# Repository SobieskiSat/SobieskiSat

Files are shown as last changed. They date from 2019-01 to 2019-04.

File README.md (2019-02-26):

# Welcome to SobieskiSat Main repository
## What is SobieskiSat?
We are a group of students from the II High School in Kraków. We got qualified for the CanSat competition, which is organised by the ESERO. Our mission is to build a can-sized atmospheric probe. The objective of CanSat competition is to develop a lot of small probes which can be used for scientific research and advancing technology.

## What is your mission?
Our mission is to build and launch a can-sized atmospheric probe, which will be equipped with basic sensors like temperature, humidity and  pressure, and also with more advanced modules like an air quality meter. In our project we also use advanced GPS positioning and RF communication using LoRa protocol.

## Repository Structure
SobieskiSat is a complex project that requires work in many fields including software, electronics, 3D-Design. That's why we divied this repository into a few directories:
  - ['docs'](docs/) - project documentation
  - ['gerber'](gerber/) - PCB gerber files
  - ['logs'](logs/) - test flights logs
  - ['models'](models/) - 3D designs
  
 ## Follow our project
 You can follow us on [facebook](https://www.facebook.com/SobieskiSat/) or visit our website <https://sobieskisat.pl/en/>
 
 ## Contact
 Contact us on Facebook or by email:<info@sobieskisat.pl>

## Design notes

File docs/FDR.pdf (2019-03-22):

# Final Design Review

### for CanSat competition

### Team

## SobieskiSat

Changelog | 2
Introduction | 3
Team composition | 3
Available resources and time management | 4
Mission overview | 4
Primary mission | 4
Secondary mission | 5
Probe description | 6
Introduction | 6
Components description | 6
Microcontroller board | 6
Batteries | 6
Atmospheric pressure and temperature sensor | 6
Particulate matter sensor | 7
Humidity sensor | 7
GPS module | 7
IMU module | 8
Gases sensor | 8
Buzzer | 9
Photoresistor | 9
Measurements | 9
Recovery system | 10
Mechanical design | 11
Weight | 11
Case | 12
Parachute | 12
Transmitting antenna | 13
Electrical design | 14
Daughterboard design | 14
Power consumption | 15
Software design | 16
System structure | 16
Data gathering | 17
Event logging and timers | 17
Data compression during radio transmission | 17
Ground station | 18
Radio receiving | 18
Ground Station Interface | 19
Landing prediction feature | 20
Data Analyzing Software | 20
Test campaign | 21
Kraków, Poland, 13.01.2019 | 1

Radio transmission tests | 21
Drone drop tests | 21
Thermovision tests - heat visualisation | 24
Project summary | 25
Resource management | 25
Budget and costs | 25
CanSat Value | 26
Sponsors | 27
Documentation | 28
Social media & promotion | 28
Facebook | 28
Radio promotion | 29
Articles | 29
Summary | 30
Education | 30
GitHub Repository | 30
Timeline | 30
Cansat Characteristics | 40

# 1. Changelog

- PDR
- Initially we planned to use an outside communication module with a chip supporting LoRa, but since it is already in CanSat kit provided to us, it was deemed unnecessary and we opted to came with some other ideas for the secondary mission.
- As of the PDR, our main goal in the secondary mission has changed. Now we are going to collect humidity and video data alongside PM density.
- In addition to the main goal of the secondary mission we also added plans to develop a descension assistance system (DAS).
- CDR
- We decided to leave out the camera because we could not find any suitable one for our needs and compatible to our board.
- We’ve updated our component list with final components we chose according to our financial capabilities and electrical requirements.
- Mission stages from PDR were modified due to software development.
- DAS (Descension Assistance System) was delayed due to prototyping restrictions and ultimately its goal was changed to predict the landing site using linear regression.

- We found that LM35 thermometer was outputting unusable disturbed data while sending via radio. Because of that we use BMP280 as our main thermometer.
- We changed GPS module to Adafruit Ultimate GPS, it includes RTC module so one planned in PDR is not needed anymore.
- Particulate matter sensor was changed to SPS30.
- FDR
- Added a new MQ-9 sensor to help analysis in secondary mission.
- We decided to increase promotion of our project in both social and traditional media.
- We finished a lot more drone drop tests than we expected to carry out at the beginning, for better analysis of data
- Descension Assistance System was finally examined and implemented into our main code.
- No more big changes were executed - we focused on developing the systems we decided to use before writing CDR

# 2. Introduction

## 2.1. Team composition

Our team consists of 5 students and our tutor, all of us are attending High School No. 2 named after King John III Sobieski in Kraków. Aleksandra Musiał - Our tutor, CS teacher and also an administrator at our school’s 3D printing laboratory.
- Jakub Czarny - Team leader & Electro-mechanical designer. His primary role is managing our progress and mission but he also specializes in electronic design and is responsible for choosing components according to our financial and electrical constraints. He is also our 3D designer.
- Andrzej Szablewski - PR spokesperson, he takes care of all PR related missions like finding sponsors, media as well as managing and updating our social media. He also works on programming and testing.
- Maciej Gamrot - High-Level Developer, he is responsible for main system development and communication with ground station. He also works on machine learning, look after our repository and develops our website.
- Damian Legutko - Embedded Developer, his job is to write code for managing data retrieved from sensors, designing backup procedures. On top, Damian designs graphical parts of our project when needed.
- Krzysztof Parocki - Digital Media Creator, he makes a photo-documentation of our progress. He also records and cuts movies based on our creation process. His work is used to promote our project in social media. He also helps with facebook site managing, testing prototypes and organizing.

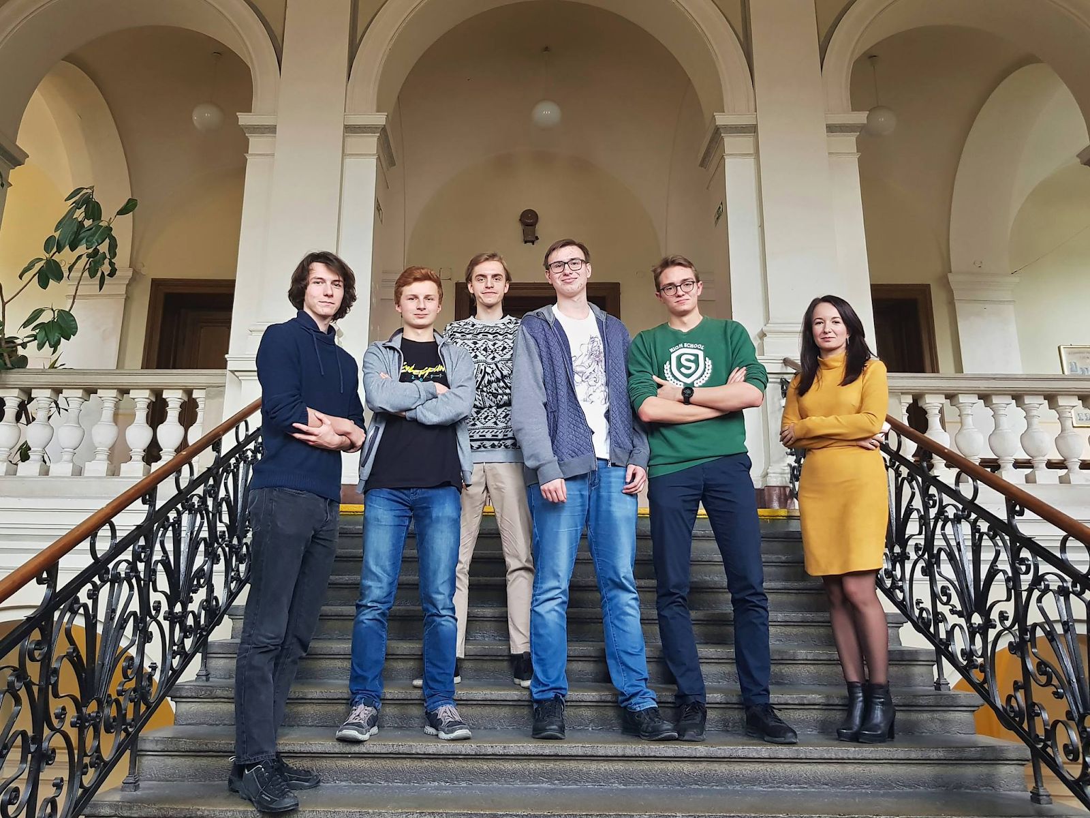
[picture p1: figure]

## 2.2. Available resources and time management

We’ve established cooperation with our school that provided us a classroom, where we hold our meetings and 3D printing lab that is under our tutor’s management. We have access to all the tools needed for the project in a public workshop - Hackerspace Kraków. Outside of the school we work on our own as well as in group through communication apps like Messenger and Discord. We meet once a week in our classroom to summarize the previous week and divide tasks for the next few days. A few weeks before completing FDR we were meeting once a week and testing our CanSat with professional drone operator.

## 2.3. Mission overview

### 2.3.1. Primary mission

CanSat mission is divided into few stages. Because of the importance of primary mission, mission stages are dependent on the time from hardware oscillator clock and photoresistor, secondary mission readings are used only as reference.
- Initialization
During Initialization, software will diagnose every component and save received data in log files on SD card. Checking if everything is working properly would prevent from errors that might occur during the mission. In this stage Can should be standing still on a flat surface for about 3 seconds because few sensors inside would be calibrating.
- Await
The Can will wait for being placed inside the rocket. Probe will occasionally collect sensor data and photoresistor readings will indicate if is put in tray and trigger next stage.
- Launch
Except for light intensity, acceleration values from IMU module would be used as reference to mission stage. Sudden acceleration during lift might cause electrical components to behave in unexpected way, to avoid possible errors most of them will go into sleep mode. If Can could not receive any data after estimated time goes into next stage.
- Fall
As a main part of primary mission, in this stage probe will collect data from all sensors, save them to SD card and send via radio.
- Recovery
Probe goes into recovery stage after estimated time or when it detects landing via accelerometer, gyroscope or GPS. It waits to be found by searching team but still is collecting data and sending radio signals.

### 2.3.2. Secondary mission

Our main goal in the secondary mission is to gain first information about atmosphere quality, disasters, and also volcanic activity. Using sensors like temperature, pressure, humidity, particulate matter density sensor as well as flammable gases and carbon monoxide sensor we can initially determine if the local atmosphere is suitable for the existence of life. Our idea in case of volcanic activity is based on dropping the satellite inside the volcano, while it’s dormant.
Particulate matter density and humidity can be used for controlling and predicting volcanic activity. Particulate matter is a very important factor in our secondary mission. Dust intensity determines chances of survival for both animal and human beings. High densities are very dangerous for life and are a direct information that the region needs evacuation. Other factors like temperature and humidity are also important as an information about life conditions. Our system can be used in fires as well as other natural disasters. The whole probe is supposed to output the collected data for the processing to happen on the ground. This allows us to quickly adapt to whatever is needed and analyze the data thoroughly.

As for launching the probe in finals we expect to test all systems and check for errors as we don’t predict the army range will output dangerous data signalyzing any disasters. The whole point of the probe is life-sensitive data collection which can be interpreted in many different ways.
In addition we will use landing site prediction software to help us understand where we are measuring and assist the primary mission recovery.

# 3. Probe description

## 3.1. Introduction

The whole probe fits in our 3D printed case. We decided to name it “Znicz1” because of the shape of our case. Our list of electrical components is now final when it comes to primary mission components and matches our needs and requirements. Every planned sensor and its function is described below.

## 3.2. Components description

### 3.2.1. Microcontroller board

We managed to test the CanSat Kit microcontroller board and decided to use it inside the probe due to its big capabilities. It completely fulfills our needs and no board change is needed.

Current status: Tested and ready

### 3.2.2. Batteries

We chose to go with 2600mAh modules (ICR18650-26FM) because we found a particular seller which would pre-weld them to a tin strip resulting in a 3P configuration of 7800mAh. This is still a massive battery pack that after a few hours of testing communication its voltage went down just 0.04V and will surely last long enough for the whole flight. Probe includes battery charger and protection module -TP4056.

Current status: Tested and ready

### 3.2.3. Atmospheric pressure and temperature sensor

This sensor fulfills all primary mission data gathering requirements, from received data we are able to calculate altitude of falling Can. The BMP280 provided with the CanSat Kit works just fine through the I

2C interface and we haven’t encountered any problems during tests. It’s also working as our main thermometer, because it’s much more stable and calibrated than the LM35. Beside its obvious function, we will use it for getting exact altitude.

Expected results: Change in temperature and pressure gives information about basic air properties and altitude. We will combine temperature with altitude. Also by this we can get information about potential disaster.

Current status: Tested and ready

### 3.2.4. Particulate matter sensor

The particulate matter sensor is our main focus in the secondary mission. Basing on data collected from this sensor it is possible to examine life conditions. We opted for the SPS30 which provides us high sampling rate of 1Hz that erases the need for slower descension.

Expected results: We expect some air pollution during final competition. It is really hard to predict the values of the pollution, but we know that on significant heights air pollution is low.

Current status: Tested and ready

### 3.2.5. Humidity sensor

Air humidity values would be used in secondary mission to predict possible fires. Very low humidity is often main cause of those disasters.
We found DHT22 sensor most suitable for our needs, it combines high precision and fast update compared to other humidity sensors.

Expected results: We expect change in humidity due to different weather. We will also analyze it in terms of altitude.

Current status: Tested and ready

### 3.2.6. GPS module

We decided to buy the Adafruit Ultimate GPS module based on MTK3339 chip. It was more expensive than our initial choice but its capabilities and big community support made it a best option. It also provided us with a RTC powered by a backup battery. We use it not only to get the exact location but also to get the altitude. It's the second source of this variable, by that we can check our data and make sure that it's correct.

Expected results: From our GPS module we will get exact position and altitude. We restricted expected values of longitude, latitude and altitude in order to get only correct values.

Current status: Tested and ready

### 3.2.7. IMU module

Accelerometer readings from this module could be used to predict earthquakes and avalanches.
Additionally IMU module will give us information about Can momentum additionally it is very useful during tests. We plan to use it when determining landing spot.
With use of special library we managed to get it working as intended. Kalman filters and Magdwick algorithm (inside DMP) used in the library give us very accurate data.

Expected results: The IMU is currently used as a backup in calculating a wind vector and we expect to see at least the full flight recorded in 9 axis.

Current status: Tested and ready

### 3.2.8. Gases sensor

Sensor responsible for this functionality is the MQ-9 module. It is sensitive for carbon monoxide (CO) as well as flammable gases. We predict that we won’t exceed the alarm levels of these gases during the mission, but this sensor is a supplement for the theoretical aspects of our secondary mission.

Expected results: Probably we won’t exceed the alarm levels of flammable gases or carbon monoxide concentration, we will get information about it live.

Current status: Tested and ready

### 3.2.9. Buzzer

The buzzer was implemented on our first PCB with a transistor as to not overload the digital pins of the microcontroller. It’s working just as expected, helping us to locate it after landing(It’s hearable from about 7-10m) and signal that the Can is working.

Expected results: We hope it will help finding our satellite after landing. It’s hearable from about 7-10m.

Current status: Tested and ready

### 3.2.10. Photoresistor

We can get information about CanSat mission stage in a very tricky way, thats by implementing photoresistor. When probe is outside the rocket it detects big amounts of light, if is inside a tray and is covered, no light shines onto photoresistor. We proved this concept during tests, Cansat was elevated inside 'Pringles’ can and ejected with special mechanism attached to drone.

Expected results: We expect that photoresistor will give us information about our can. We will know is it inside or outside the rocket.

Current status: Tested and ready

## 3.3. Measurements

Table below presents data that will be gathered during the mission. Minimum and maximum columns represent predicted values to be received. Readings precision is presented in Significant figures column with format: [before ; after decimal point] in base 10.
Sensor | Reading variables | Minimum | Maximum | Significa nt figures | Samplin g time [ms]
2C) BMP280 (I | Pressure | 600 hPa | 1100 hPa | 4 ; 1 | 40
| Temperature | -10°C | 40°C | 2 ; 1 | 40

Adafruit Ultimate GPS (UART) | Latitude 1 | 49,00° | 52,00° | 2 ; 7 | 1000
| Longitude 1 | 14,07° | 24,09° | 2 ; 7 | 1000
| Altitude | 0 m | 3000 m | 4 ; 1 | 1000
| Clock | mission start time | mission end time | - 1000
DHT22 (Digital communication) | Humidity | 0 % | 100 % | 2 ; 0 | 2000
| Temperature | -10°C | 30°C | 2 ; 1 | 2000
SPS30 (UART) | Mass concentration | 0.3 μg/m³ | 100 μg/m³ | 2 ; 1 | 1000
| Number Concentration | 0.3 1/cm³ | 10 1/cm³ | 1 ; 1 | 1000
MPU 9250 (I 2C) | Tilt | 0° | 360° | 3 ; 2 | 20
| Acceleration | 0 g | 4 g | 1 ; 2 | 20
| Magnetic orientation | 0° | 360° | 3 ; 0 | 30
Photoresistor (Analog) | Light intensity | 0 lux | 10 lux | 1 ; 2 | 10
MQ 9 (Analog) | Flammable gases and carbon monoxide | 0 | 1024 | 4; 0 | 10

1Minimum and maximum values of GPS location are set to Poland boundaries. During the real mission they would not reach further than few kilometres from start. This allows us to compress data more effectively

## 3.4. Recovery system

As described in 3.5 and 3.5.3 we are using a parachute made by us and then calculated and tested for falling with a speed of 9m/s. It’s attached to the body with 8 strings with a holding strength of 60kg. They are attached by pinching them through 8 holes and tying a knot. So far our test have proven this design successful.
The main power switch is located at the bottom and is a simple bistable slide switch. (See 3.5)

## 3.5. Mechanical design

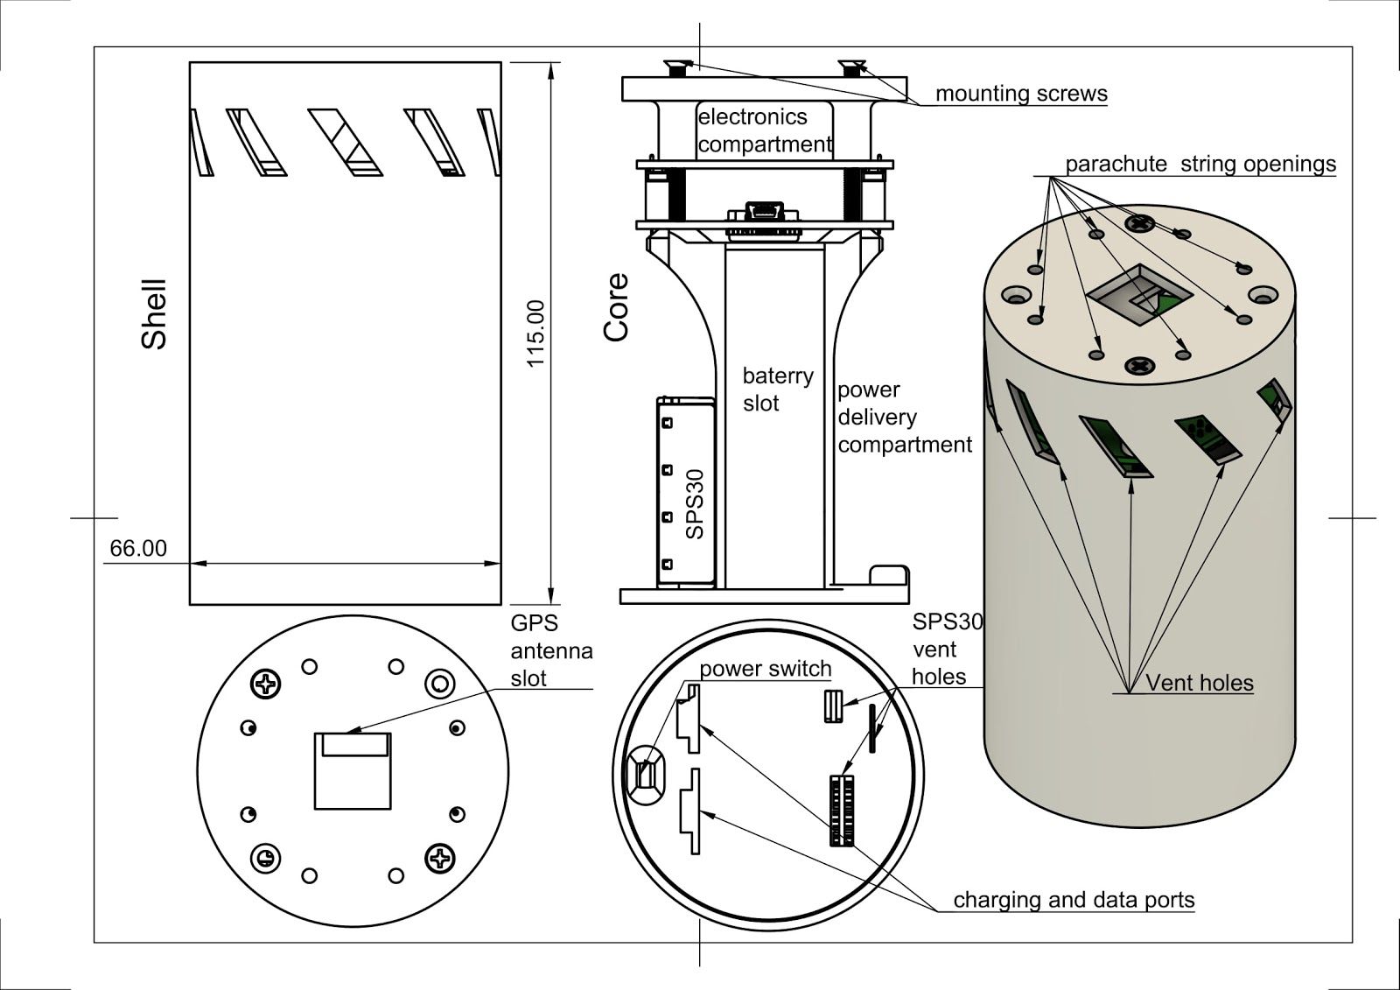
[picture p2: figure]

Open link to the full assembly: https://a360.co/2CFqlhm

### 3.5.1. Weight

Our full assembly was weighed firstly on a kitchen scale then in our school chemistry lab and both reported it being safely under 350g, about 336g.

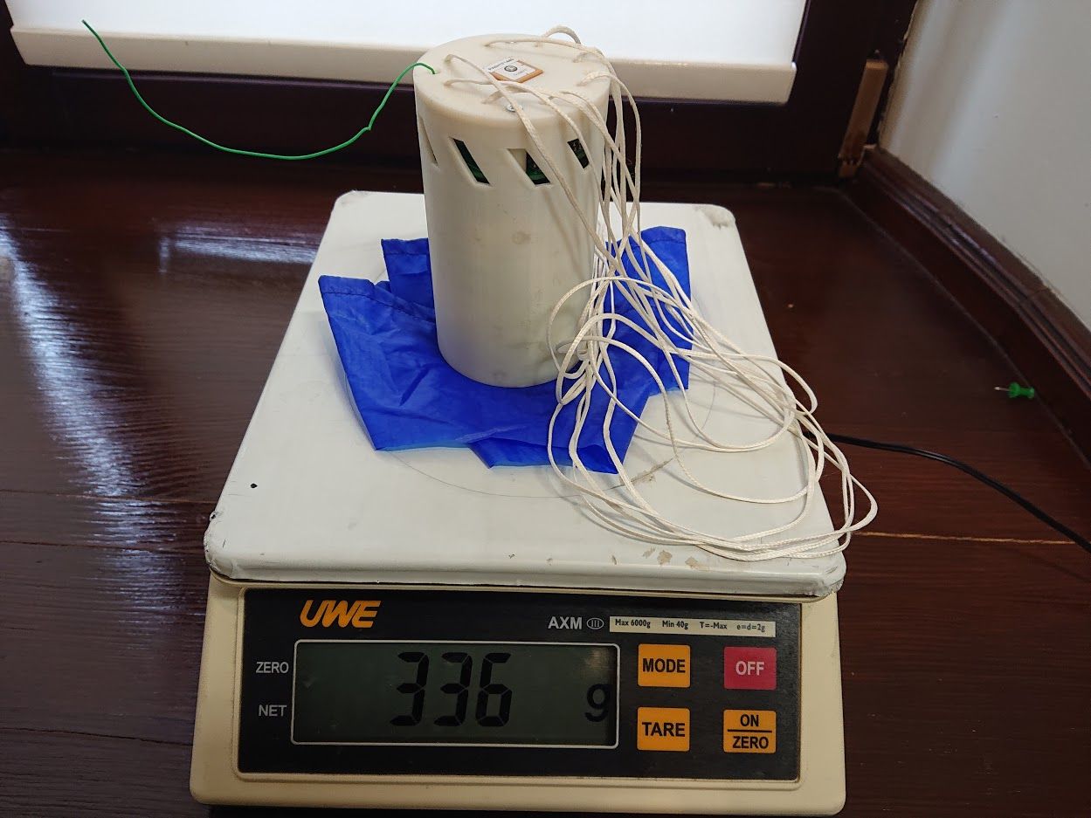
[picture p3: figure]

This picture shows the final weigh without the MQ-9, but its weight is only about 5g.

### 3.5.2. Case

The Case is made of a ABS based material called Z-UltraT and 3D printed in our school. The iterative design lead us to a very efficient and strong assembly, which is held together by 2 M3 steel screws. The center of mass is located fairly low which helps stabilize everything during flight. During our tests, the design withheld falling with a tangled parachute(vmax~15m/s) without any structural or electrical damage.

### 3.5.3. Parachute

Our first real parachute prototype made out of Skytex 27 Classic had a radius of 20cm with an 8 cm in diameter center hole. This was an overestimation(theoretical r=18 cm, Cd=0.78) for test purposes and resulted in vmax=5.5m/s.

After adjusting the drag coefficient according to our test flights (Cd=1.26)

the parachute was modified to a radius of still 20 cm but a center hole with a diameter of about 13cm. Testing the new version resulted in safe vmax=9m/s which meets the required range of 8 to 11 m/s.

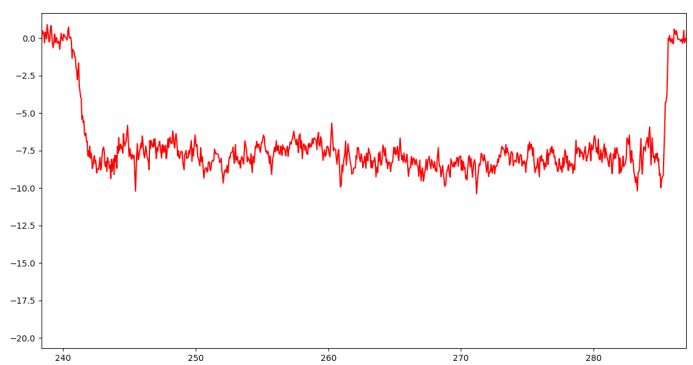
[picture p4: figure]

This graph, generated from data gathered during drone mission, represents speed calculated between 2 heights of 10 pressure readings apart, in relation to time. The distortion is caused by a low distance between readings in the calculation program, but shows the overall speed more accurately.(it’s showing a negative value, because it’s calculated by a decreasing height)

### 3.5.4. Transmitting antenna

For the transmitting antenna on the can we used a 17 cm long solid core wire soldered directly into the microcontroller board. So far it suited its purpose but in case of it being not enough we can replace it with a manufactured one.

## 3.6. Electrical design

### 3.6.1. Daughterboard design

We designed and ordered a printed circuit board for all of our main sensors and components as a shield for the CanSat kit. As it was made in a hurry so it had some bugs, but after soldering a jumper wire to connect the buzzer transistor to a correct port it was fully functional and behaved as expected in all of our tests. After adding a new sensor to help our secondary mission and additional functionality like battery voltage monitoring, reset switch, stress relief holes and better spatial arrangement we ordered a new pcb and are expecting it to arrive shortly. It’s important to note that the new PCB has retained its core functionality with the old one and even in case the added features not working, it should behave completely the same in regards to our tested design.

New PCB schematic and design:

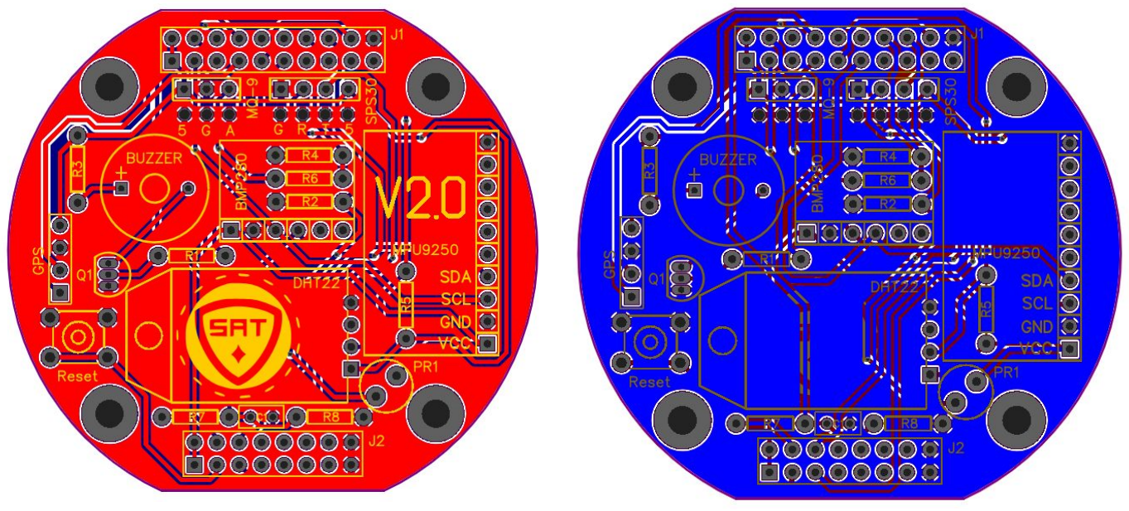
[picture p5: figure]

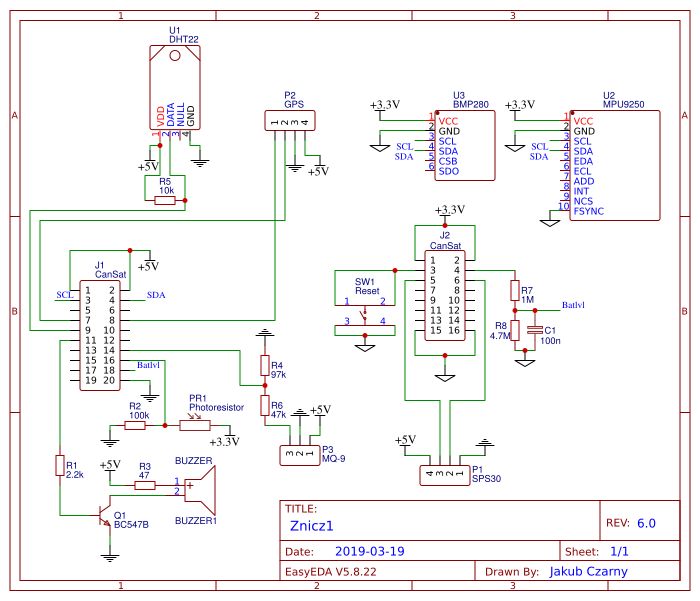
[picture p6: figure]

### 3.6.2. Power consumption

Here is the theoretical maximum power consumption e.g. worst case scenario.
Component | Maximu m current draw [mA] | Voltage [V] | Efficiency 2 [%] | Effective power [mW]
Microcontroller | 20 1 | 3.3 | 50 | 132
SX1278 | 120 | 3.3 | 50 | 792
BMP280 | 1 | 3.3 | 80 | 7
SPS30 | 80 | 5 | 80 | 500
DHT22 | 1.5 | 5 | 80 | 9,4
Adafruit Ultimate GPS | 25 | 5 | 80 | 156,3

MPU9250 | 3.7 | 3.3 | 50 | 24,4
Buzzer | 20 | 5 | 80 | 125
MQ-9 | 150 | 5 | 80 | 937,5
Total | 421,2 | - | - | 2683,6

Photoresistor is drawing an unnoticeable amount of current so we decided to skip it in the calculations

1 - Here we used the average values provided in the CanSat Kit documentation, because we think they are more suitable and we couldn't find the maximum power draw for the microcontroller.
2 - Efficiency is based on which power source is used by the component and it’s either 80%(Efficiency of the step-up converter) for +5V or ~50%(80%*66% -combined efficiency of the step-up converter and line regulator) for +3.3V

Battery capacity = 2600mAh*3*3,7V = 28860 mWh Total power consumption = 2683,6 mW Theoretical maximum operational time = ~10,8 We do not have an onboard battery voltage meter yet so we couldn’t make a continuous battery drain test, but since getting our batteries we only charged them once to full capacity and after using them for all tests during the last 2 months the voltage dropped to only about 3.9V making them safe for the required 6 hours of ontime.

## 3.7. Software design

### 3.7.1. System structure

3.7.2.

Whole functionality of all the components

included inside probe is contained inside separate library. As a result main code uses only objects of probes components and their basic methods like: begin, update etc.

For every sensor inside probe, there is a class with defined data reading methods that inherits from abstract Sensor class.
Sensor class consists of initialization and update methods, radio and SD buffers, diagnosis variables and update time. Software structure like this allows to use every sensor in unified way without worrying about it's other methods required for proper working.

### 3.7.3. Data gathering

Every sensor has different specifications and by that every has its own update time, to not lose data while waiting for those with low sampling rate, sensors are invoked asynchronously when their update time expires. With every measurement sensors input new reading into their SD buffer and every reading is marked with hardware clock time. For example BMP280 saves pressure and temperature floats
and GPS saves last received NMEA sentence.
Methods responsible for data gathering are
different for every one of them but their outputs are later unified to fit Sensor base.
Every session of CanSat being active is saved to different directory on SD card. Inside those directories there are files belonging to every sensor. Example file is presented on image on the left.

### 3.7.4. Event logging and timers

Our CanSat software implements functions responsible for logging too. Every important action inside probe will be saved with time marker on .txt log file.
By time marker (number after ‘@’ char) in CanSat we understand value of millis() function that returns amount of milliseconds elapsed since board start counted by the hardware clock. Additionally software gets current time from RTC module inside GPS board. At the beginning of log file there is an information about real time and time marker during this moment. Example heading of a log file: #110119161503412@1302
This string lets us know exact day, month, etc.. and time marker during this moment. Every action after this line will be marked only with time marker because we can simply add difference of elapsed milliseconds to get event time.

### 3.7.5. Data compression during radio transmission

Probe software implements simple yet effective data compression. In connection with optimal LoRa variable settings we are able to transmit real-time readings with sending frequency of 5,3 transmissions per minute

(look at: drone tests 3 & 4) and could be freely changed to any value above by sending queued data (but in reality only pressure sensor is able to update so fast). Our compression bases on mapping to known region of numbers and transmitting only changed variables.

Measurement values collected from sensors would be mapped to some binary number with length specified by reading precision. For example knowing that temperature is in range of -10 to 30°C and reading precision is: two digits before and one after decimal point, we can map value from 0 as -10.0°C up to 400 as 30.0°C. Numbers in that range can be represented as binary number with length of 9 bits. During compression a data format is created.
Example data format (must be identical for receiver and transmitter):

1 0_26_Latitude_49.0000000_54.5000000_2_7 26_53_Longitude_14.0699997_24.0900002_2_7 53_67_Altitude_0.0_1000.0_4_1 67_90_Pressure_600.0000_1200.0000_4_4 90_103_Temperature_-20.00_50.00_2_2 103_113_PM25_0.0_100.0_3_1 113_123_PM100_0.0_100.0_3_1 123_128_PackNo_0_32_2_0 X

Example data send:

Later received data will be decompressed on ground station and presented in human-readable form. Our first tests of compression during real mission achieved shortening packet from 54 Bytes (chars) to only 16 Bytes. Algorithm still can be improved but for current phase we have already reached the point where not many sensors could be updated before there is time to send another packet.

# 4. Ground station

## 4.1. Radio receiving

Antenna:
Our base station antenna (LPRS | YAGI-434A) | was ordered from UK and
works without any problems. It already was equipped with an SMA connector so no modifications were necessary. Its aluminium construction makes it very light and easy to handle which helps make it handheld. in order to verify the connection with our satellite without having to observe computer screen we redesigned and 3D printed the antena handle adding small OLED screen that displays the most important data - RSSI, height, etc. After installation it performs exactly as intended enabling operating antena by only one person.

Data received by the receiver is decompressed, saved to SD-Card and outputted to a serial port. Software ran on the computer connected to the receiver via USB will listen for input. Read data will by parsed, displayed and subjected to further analysis. Each input will be also saved by saved by DataManager and logged by EventManager.

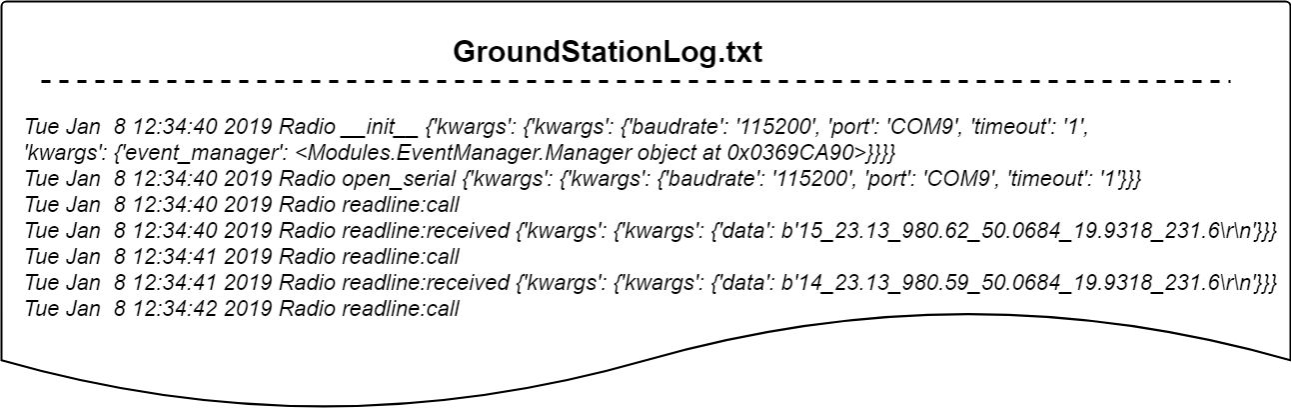
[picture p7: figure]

## 4.2. Ground Station Interface

We divided main window of ground station graphical interface into a few groups:
- Information Board display live information from satellite (temperature, humidity, etc)
- Interactive Gyroscope Widget informs about the inclination of satellite relative to the ground by processing data from GPS
- Interactive Map Widget plots current and past location of satellite creating the flight path of our satellite. Each point is colored depending on RSSI and can be clicked to display further information about satellite at that moment. Additional feature we developed is Landing Zone Prediction System, which forecasts landing spot based on current wind vector measured during flight and wind data obtained from internet.
- Group of buttons used to control DataSaver and change information displayed on plots.
- Interactive graphs plotting live data from satellite.

### 4.3. Landing prediction feature

We succeeded to implement Landing Prediction Zone System which receives GPS data and presents the probable landing spot. We calculate this zone depending on current wind vector, live wind data from internet and terrain elevation. The prediction isn’t very accurate (the miscalculation equals approximately 10% of the drop altitude).
We plan to implement landing prediction feature into our ground station software. So far we found linear regression methods as the best candidate. From received GPS data we are able to represent the Can’s route as a line in three dimensional space. Having known ground altitude we can solve the linear equation and get the predicted landing position. The results definitely would not be very accurate, in the future we plan to also use IMU data providing we find proper methods to use them.

### 4.4. Data Analyzing

We have finished implementation of analyzing features to our ground station software. The main ideas are that after flight probe can be plugged to the computer for analyzing information saved on SD Card as well as data saved on computer by DataManager. Software will enter Debug Mode in which every measurement will be presented in a window similar to the one with live data, but with feature to reenact flight history in a real time and readout by readout. All information will also be compared and analyzed with regard to irregularities and interferences. After analyzing all plots can be saved as pictures, simplifying the preparation for the results presentation.

# 5. Test campaign

## 5.1. Radio transmission tests

- 18 December - 2.8 km of range
- 26 February - 6.8 km of range
We tested our radio transmission between Piłsudzki’s Mound and the Roof cafe of Music Academy in Krakow, as shown below.

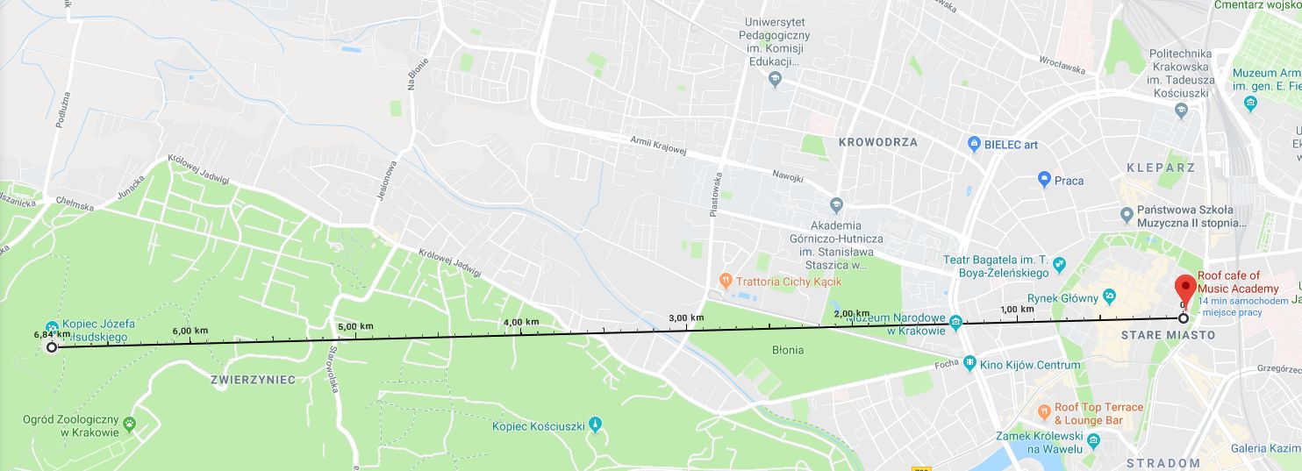
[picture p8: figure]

At this distance we measured a max RSSI of -119 and the connection was stable. We were sending uncompressed packets with all gathered sensor data.
- 6 March - first model of compressed transmission allowed us to send same data about 3 times faster as before.

## 5.2. Drone drop tests

We cooperated with FlyTech to perform our drop tests.
- 11 February - Our first paratuche prototype achieved 5.5 m/s fall speed. Probe was sending pressure, temperature and position data, that's 33 Bytes with about 2.5 transmissions per minute. Unfortunately we were not able to use radio and SD at the same time, board was crashing in random moments. We managed to make 5 drops, one with only radio transmitting and rest with only SD logging.

- 26 February - Our daughter board arrived, so we could implement few other sensors and test new mechanical design. This time probe was sending additionally particulate matter density values. Still problem with crashing wasn't solved, our main goal this day was to test ground station interface so we made 4 flights with only radio transmission. It was the first time when the buzzer was used, because it wasn't making enough noise we managed to lower resistance of safety resistor.
- 6 March - This time SD card and radio finally worked, we build new parachute with about 10 m/s falling speed. New data compression algorithm allowed us to send much more precise GPS data and with higher speed.During the last flight that day our can landed in a small river and we focused on recovery and testing every part. After drying we have found two of our sensors to be broken - SPS30 and DHT22, after cleaning the SPS30 got fixed and only the DHT22 remains to be replaced.

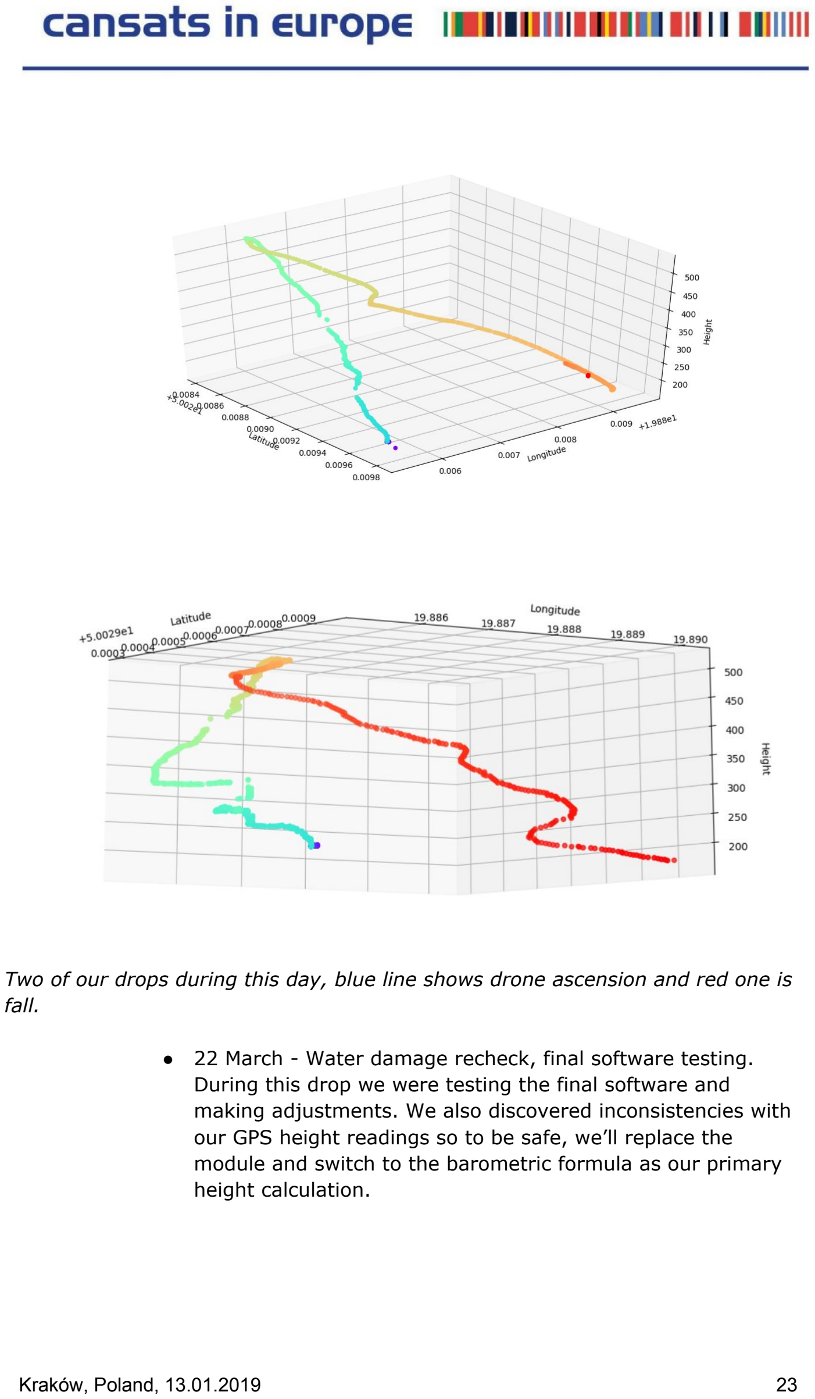
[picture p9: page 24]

Two of our drops during this day, blue line shows drone ascension and red one is fall.

- 22 March - Water damage recheck, final software testing. During this drop we were testing the final software and making adjustments. We also discovered inconsistencies with our GPS height readings so to be safe, we’ll replace the module and switch to the barometric formula as our primary height calculation.

## 5.3. Thermovision tests - heat visualisation

We decided to check our satellite in terms of heat emission. It is important factor because heat emission can disturb measurements like temperature or humidity. We checked all modules which can emit heat. The measurements were made with a professional thermal imaging camera. Our probe was running for over one hour before taking these thermal photos but we were also checking its state during this hour. The environment temperature is about 22 °C, so it was initial for all sensors. The temperature of the most important spots after one hour is presented in table below. (+ fotki)

Module | Average temp. | Hottest point
Adafruit Ultimate GPS | 28,1 °C | 36,8 °C
CanSat Kit Motherboard | 25,6 °C | 29,2 °C
SPS30 | 23,7 °C | 24,8 °C
Batteries | 22,2 °C | 22,4 °C

We also present some images from the camera. All sensors were visible to the camera - cylindrical cover was taken down.

## 6. Project summary

## 6.1. Resource management

### 6.1.1. Budget and costs

Note: All prices in this section to the 8th point are converted from PLN to EUR with exchange rate 1 PLN = 0.232996887 EUR (05.01.2018 - Google)

Note: All further prices in this section are converted from PLN to EUR with exchange rate 1 PLN = 0.232503288 EUR (22.03.2019 -Google)

We have started with 267,95 EUR. We hope we will get more money and partners. Now we are on a good way to get a sponsorship from Kraków Airport. On this day (22.03.2019) our spending is presented in the table below.

No. | Our expenses | Price (EUR) | Category
1. | website hosting | 4,66 | Promotion
2. | Facebook advertisement | 5,82 | Promotion
3. 2x Charger TP5056, 2x Buzzer, 1x DHT22 and | shipment | 7,47 | Modules
4. 1x MPU9250 sensor, 3x batteries, welding service | and shipment | 21,64 | Modules
5. | 1x Adafruit Ultimate GPS and shipment | 38,09 | Modules
6. | Antenna and shipment | 53,42 | Modules
7. | Electrical tape, sandpaper | 1,05 | Modules
8. | Food, snacks, drinks for meetings | 31,43 | Meetings
9. | Stickers | 6,97 | Promotion
10. First PCB, screws and M3 rod, OLED screen and | shipment | 32,63 | Modules
11. Sockets, Nanoprotec spray, MQ-9 sensor and | shipment | 23,63 | Modules
12. | New PCB (planned to insert, in shipment) | 12,24 | Modules

SUM | 239.05

Now we have 267,95 - 239,05 = 28.9 EUR. Our main planned expense is a new GPS sensor, in case of a possible breakdown of the prior one during the finals. The next thing is the eventual cost of the participation in the final for the fifth member of a team. We are clear to sign the contract with Cracow Airport, so we will possibly get some additional financial resources for our project from this source.

### 6.1.2. CanSat Value

Note: All prices in this section to the 9th point are converted from PLN to EUR with exchange rate 1 PLN = 0.232996887 EUR (05.01.2018 - Google)

Note: All prices shown further are converted from PLN to EUR with exchange rate 1 PLN = 0.232503288 EUR (22.03.2019 - Google)

The whole value of our CanSat is presented in the table below.

No. | CanSat part | Value (EUR)
1. | Adafruit Ultimate GPS | 34,92
2. | Batteries and welding service | 11,87
3. | MPU9250 | 7,69
4. | DHT22 | 3,69
5. | Buzzer | 0,47
6. | Li-Ion Charger | 1,21
7. | SPS30 | 40,93
8. | Case - 80g Z-ULTRAT material | 4,66
9. | Parachute and cords | 5,00
10. | PCB | 0,17
12. | Screws, M3 rod | 0,55
13. | MQ-9 sensor | 6,89
14 | USB Socket | 0,45
| SUM | 118,50

### 6.1.3. Sponsors

Note: All prices in this section are converted from PLN to EUR with exchange rate 1 PLN = 0.232996887 EUR (05.01.2018 - Google)

We wanted to amp up our chances for getting a sponsor so we have written to the following companies:
Comarch, Asseco, Cd projekt, Orange, Play, Coca cola, Pepsi, Rmf fm, Ailleron, Shell, Orlen, Lotos, Arge, Tvn, Radio zet, Tok fm, Kraków Airport, Codewise, Flytech UAV, Kraksky, botland.pl, School parental council, Company which want to be anonymous.

We have several sources of money as well as partnerships. They are presented in the tables below.

No. | Source of money | Amount (EUR)
1. | School parental council | 186,40
2. | Team contribution | 58,25
3. | Team advisor contribution | 23,30
| SUM | 267,95
No. | Partnership | Our benefits
1. | Our school | We have unlimited access to our school’s 3D printing lab
2. | Botland.pl | We got a 7% discount on all their items
3. Company | which wants to be anonymous | We got parachute material and parachute cords -The material is called DOKDO-N20DMF-WR-HD38
4. Kraków | Airport | We are clear to sign the contract with the airport. After signing it we will get 800 PLN. The contract has been accepted by both sides - our school and Kraków Airport.

## 6.2. Documentation

### 6.2.1. Social media & promotion

6.2.1.1. Facebook
We have over 400 likes on our Facebook account (linked below). Posting regularly about 35 posts, we have on average 400 views under every single one. We have also several posts with about 1000 views, and also one, promoted, with nearly 8000. This post is a movie-type which is a vlog from our first radio transmission tests. By doing this, we wanted to promote our project as well as the whole competition among the local and school community. Our facebook profile contains valuable educational information and presents the whole timeline and advance of our project. Recently we also published a very special movie - our advertisement. Our predictions say that it will be the most viewed post ever on our profile - 3 days after release it has over 8000 views.
6.2.1.2. Radio promotion
We have also written emails to local radio stations. Many of them replied and invited us for short broadcasts. During these conversations we were talking about our project and its educational values. Table below shows radios we have already visited and our plans for future.
Radio name | Status
Radio Kraków | Visited 03/12/2019
Radio Eska | Visited 03/18/2019
Plus Radio | Visited 03/18/2019
Radio Wawa | Visited 03/18/2019
Antyradio | Visited 03/21/2019
Melo Radio | Visited 03/21/2019
UJOT.FM | Planned live on 03/25/2019
Radio Pryzmat | Planned live on 04/10/2019

6.2.1.3. Articles
We have also written many articles for magazines and newspapers. Our main target is to show that technology is interesting and encourage people to follow our project. Table below shows magazines we have already written for.
Magazine/Newspaper | Status
Life In Kraków | Published
PC World | Published
Gazeta Krakowska | In progress
AntyWeb | In progress
21. Wiek | In progress
6.2.1.4. Summary
Due to the project promotion we got huge hype. Beside these actions, we promoted ourselves on our schools facebook group which has over 3000 members as well as school webpage with over 2000 daily entries.

Facebook site:
https://www.facebook.com/SobieskiSat/

### 6.2.2. Education

We also plan to make some workshops for other students from our school. We are going to make a presentation about our project and present how our satellite is working. These workshops will probably take place during the next week after completing FDR. Probably we will also have a chance to speak in front of the students applying for our highschool during the “open day”. We plan to show basics of our project as well as introduce students to the CanSat world.

### 6.2.3. GitHub Repository

We decided to create a public organization in github, so that everyone interested in our project could follow our progress. You can find there the entire code of the satellite and ground station. We also include all 3D models, diagrams and documents of our project. This helps to organize and archive all of our work, enabling easy tracking. Satellite, Antenna and ground station softwares are updated there regularly.

Our GitHub: https://github.com/SobieskiSat

### 6.2.4. Timeline

### 26 September – The date of one of our first actions taken to

develop our micro-satellite. This day we finally got access to the school 3D lab, where we printed the first case to see exactly how much space we do have to fit in all components. We have also mentioned this action in PDR, as one of the Project Summary.

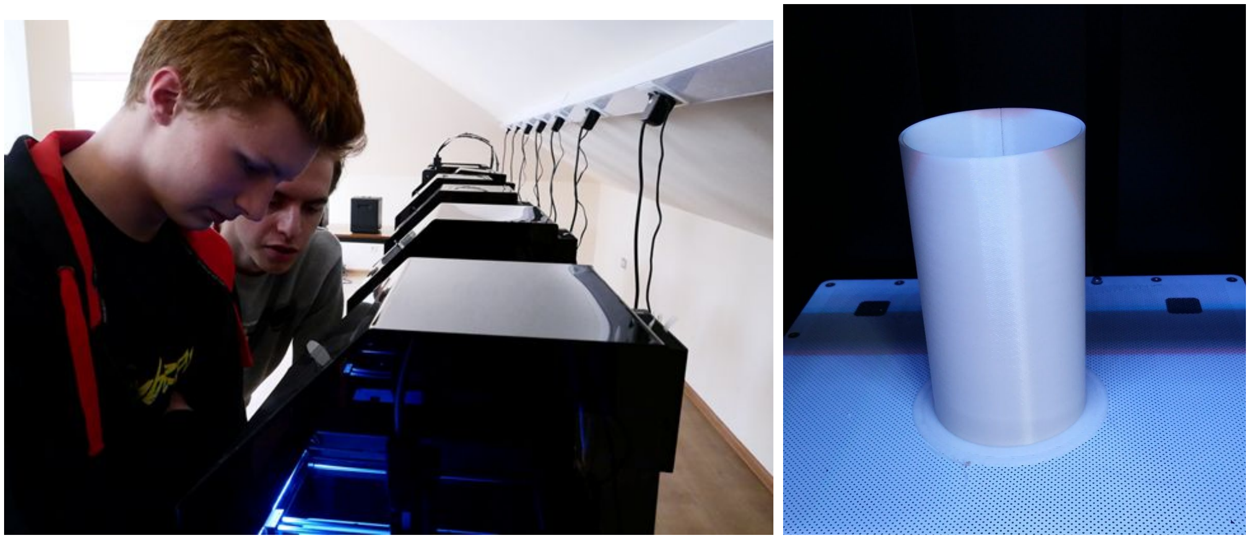
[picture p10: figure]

### 30 September – that day we met with the airplane pilot, who

helped us to design and plan a lot of thangs attached to aerodynamics and electronic circuits. We elaborated a project of components composition inside the case, spoke a lot about secondary mission idea and chose the way which our marketing and advertising actions will follow in the future.

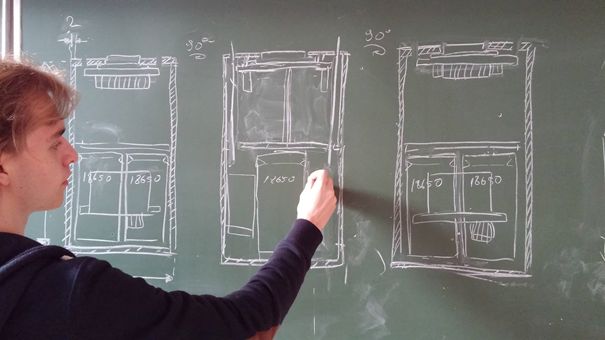
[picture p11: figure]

### 20 November – our first meeting

during which we were testing modules we had received a couple days before. We have tested
components | such | as
accelerometer, | gyroscope | and
magnetometer, | simultaneously
with | other | essential modules
needed to complete the primary
mission. All gages of these we

have done on a breadboard, but after that we still needed to wait for missing parts.

### 27 November – that was our second meeting during which we

worked with modules, provided to us a few days after the first meeting. We finished the attunement of the GPS module, and we plugged in the same time every other module to see if it will work correctly – the only one missing was particulate matter module, which we planned to add and trial at one of our future meetings.

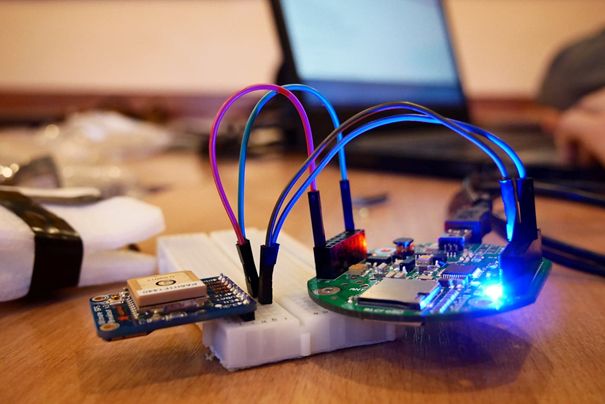
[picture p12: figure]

### 11 December – Our measures to

design a first prototype were over. We printed a new case for our modules, this time it was more durable and contained a top, so that we could close components up inside. We fitted in all modules needed to complete primary mission and some from secondary and wrote a code to be able to send data from the can and receive it in our ground station, so the first prototype
was finally ready to try.

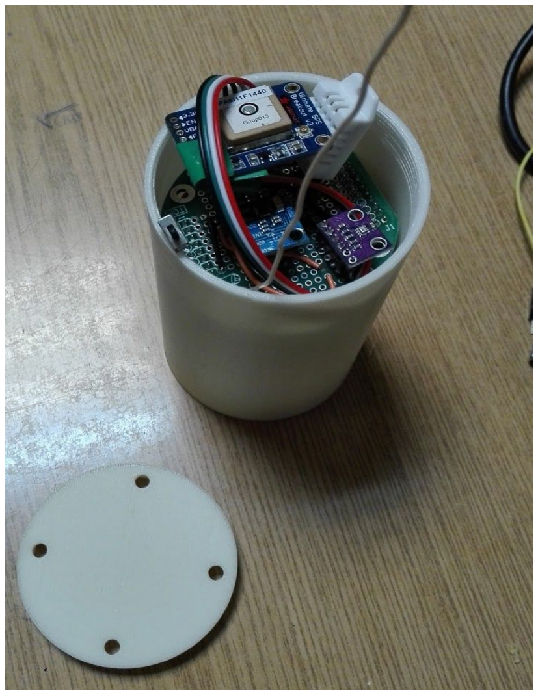
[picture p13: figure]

### 13 December – we got an high-range aerial ordered a week

before, that we needed to receive data from our can and relay it further to the ground station. We did a few adjustments in our code to meet the aerial requirements and make everything work correctly, and decided that we need to probe the real aerial range to check if the signal will work during the final competition.

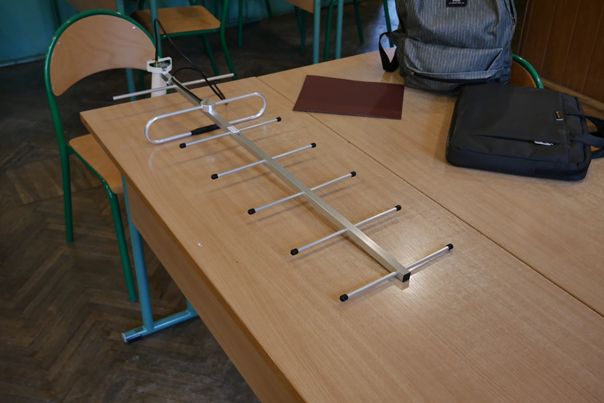
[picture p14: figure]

### 18 December – The day of trials. We were testing our aerial range

for about 4 hours, by leaving the ground station in the northernmost part of Błonia, and walking away as far as we could with our sender. We have reached 2,8 km distance, without a big loss of signal, hence we were certain that out satellite will be transmitting data all the time during the plummeting at the finals. That day we have also completed our stab at cansat falling with parachute. Full report of our efforts was posted on our facebook page as a vlog and animation of our repositioning.

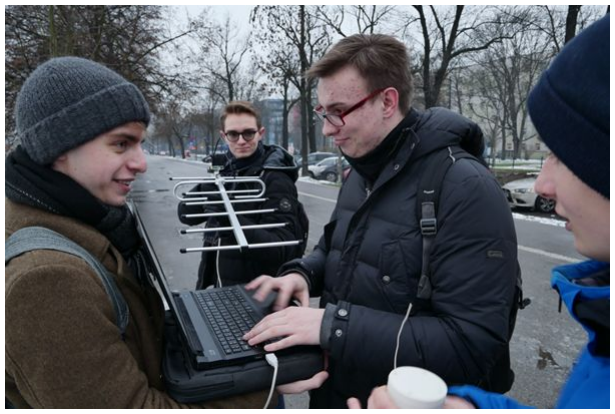
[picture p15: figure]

### 23 December – The first usable prototype of the parachute was

done. All measurements and calculations had been completed, and afterwards the plastic foil was cut and formed.
Work on the code was also going forward that day.

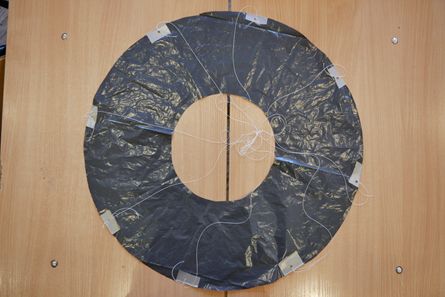
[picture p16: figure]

### 8 January – We have 3D printed a new version of the case with

some improvements, for example holes to provide better air-circulation and new latch system to test new ways of joining the two halves. We have also thrown it with a parachute out of a balcony to check if it will fall properly without destroying itself.

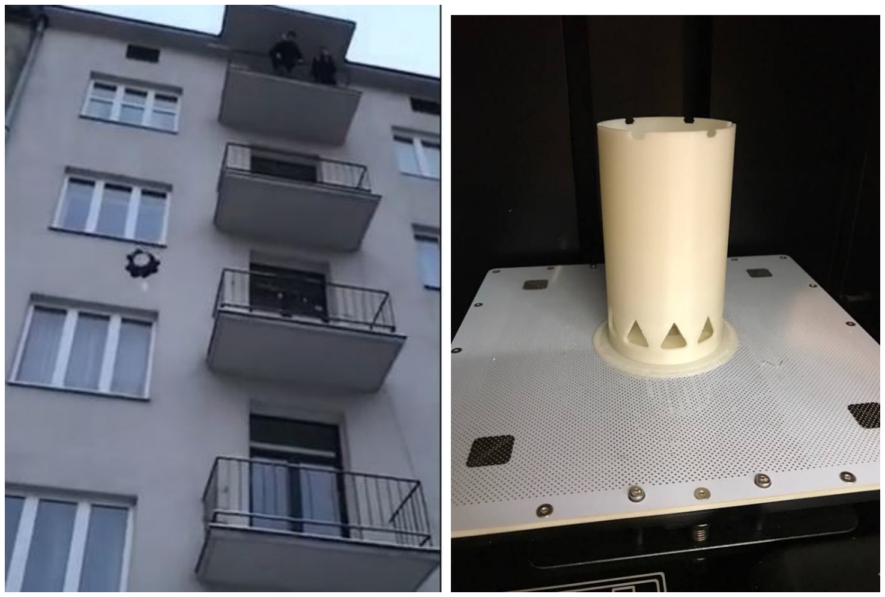
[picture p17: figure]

### 11 January – Parachute material was finally with us, provided by

the company which wants to stay anonymous – we got over six times more material than we wanted, which enabled us to make multiple versions and test each one separately. We’ve also set up our Github page.

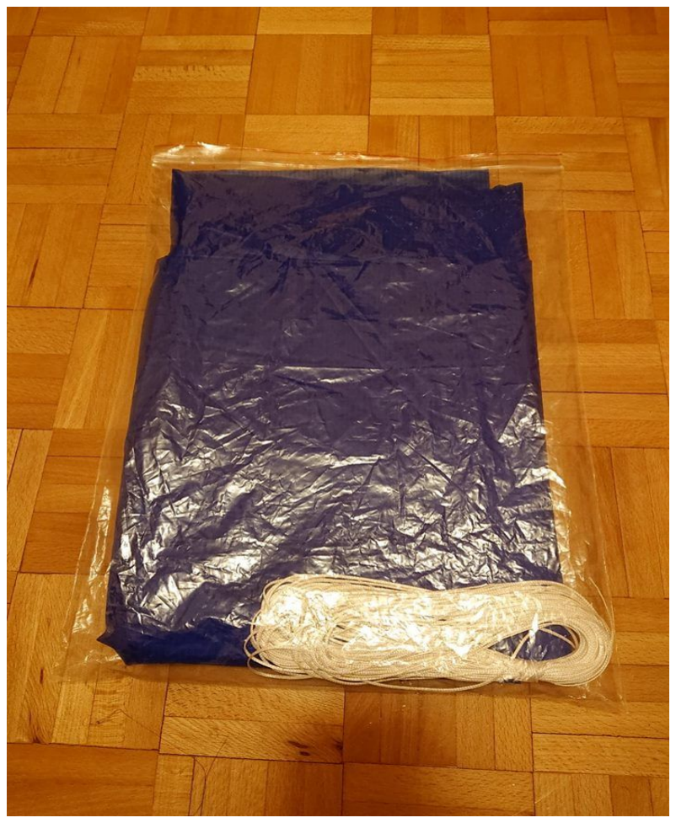
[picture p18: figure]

### 29 January – We had an opportunity to test our parachute for the first

time. Before we could do it, we had had to give a parachute material to the cobbler. We needed to conform and cut cleanly our material. Scissors wasn’t enough, because we wanted to do that as precisely as we could.

We threw it from the 4th floor of a residence hall of one of our team members.

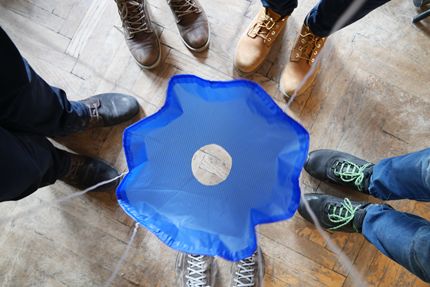
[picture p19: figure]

### 5 February – We got a particulate matter (PM) meter from our friendly

cansat group from Cracow – Plastic Monkeys! We checked if everything works correctly, and then we fitted it to our satellite.

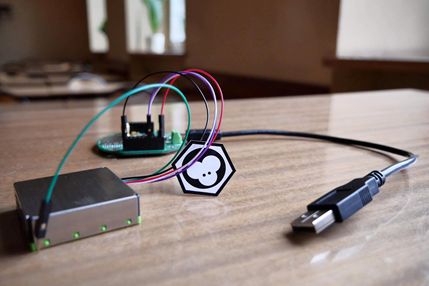
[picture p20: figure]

### 11 February – We tested our satellite by throwing it from a drone with

full number of sensors inside for the first time. We had some difficulties with the parachute, what caused one fall without any air resistance. However, it turned out our unit is almost unbreakable, because there weren’t any grooves on a casing. During these tests we had a still radio connection with our satellite and we were constantly receiving data. We were also saving readings gathered by all of the componentry on a

SD-card inserted into the unit. All that we could achieve due to a courtesy of the FlyTech UAV company.

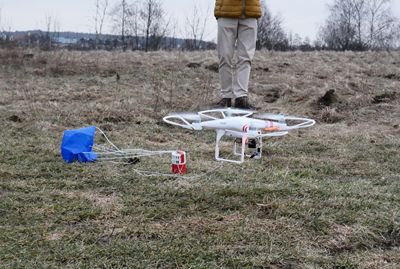
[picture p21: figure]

### 18 February – After a long time of a delivery from China and an

adventure with a lost package, we finally got our self-designed, printed circuit board! It solved a problem of ubiquitous wires, which furthermore have their weight. It was fitting in perfectly in our casing, so we attached all the components to it as soon as we could, and prepared our satellite for further drops from the drone.

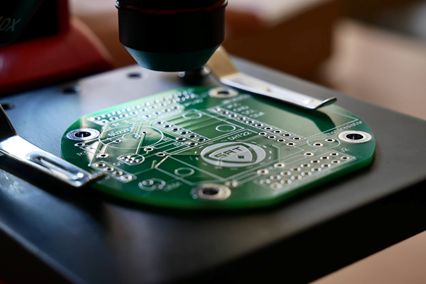
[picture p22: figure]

### 26 February – One of the most important days for our project. It was

the second time when we were dropping satellite from the drone.

However, that day, we elevated our piece of work to over 300 (before, it was only 170) meters! We were simultaneously logging and live-displaying the readings gathered by sensors working inside our satellite. Everything was working correctly, the only things we had to do were a few software adjustments. Later that day, we eventually examined the signal of our aerial – we divided ourselves into two groups, one travelled to the Piłsudski’s mound with the satellite, and the other went on the roof of Cracow Music Academy. The distance between these two areas totals 7 km, but transmitting was working perfectly. We were almost sure, that our unit is in the final stage of production. Moreover, a part of this day was shown in the second Vlog!

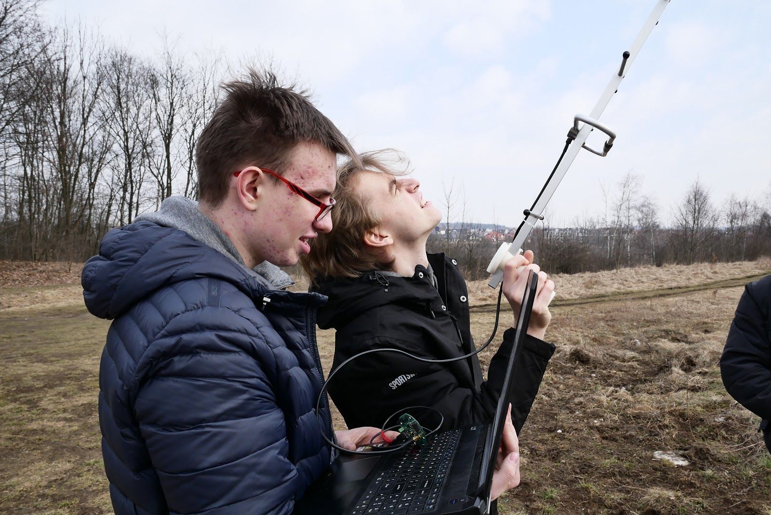
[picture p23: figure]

### 6 March – The third day of satellite drone test. We were working on the

landing prediction feature we want to implement, as it was said in the secondary mission description, but we weren’t lucky – during the trials our satellite fell into a river, which has only one meter in width. We were terrified, but it turned out that our gear is also waterproof – just a few of the components were destroyed!

### 10 March – We started considering about promoting ourselves in the

traditional media, not only on a facebook page. We wrote a lot of e-mails to the most of radio stations in Cracow, and also to internet newspapers. We got a lot of positive answers inviting us to take part in radio broadcasts, as well as propositions of writing articles for the newspapers, such as PC World and LifeInKraków.

### 14 March – The day of recording a short film, which we want to promote

and reach as many people as we can. We recorded brief interviews and then cut a movie – We posted and promoted it on Monday. For now, it has about 11.000 of reach and 4.000 views.

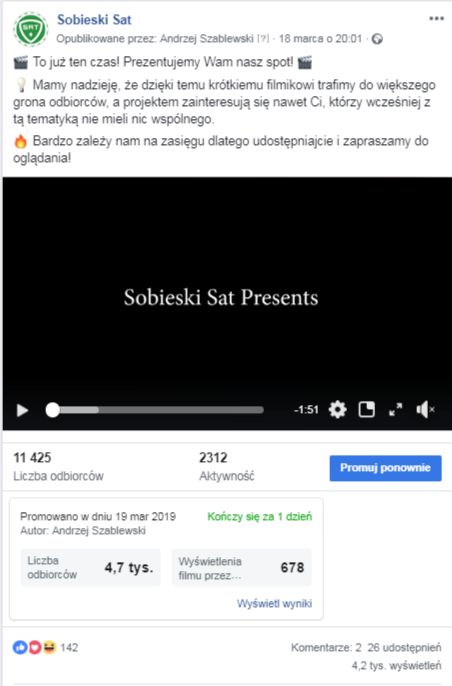
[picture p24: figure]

## Cansat Characteristics

Characteristics | Figure
Height of the CanSat | 115mm
Diameter of the CanSat | 66mm
Mass of the CanSat | 341g
Estimated descent rate | 9m/s
Radio transmitter model and frequency band | CanSat Kit SX1278
Estimated time on battery | ~10h
Cost of the CanSat | 118,50 €

CanSat layout without cylindrical cover

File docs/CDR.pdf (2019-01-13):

# Critical Design Review

### for CanSat competition

### Team

## SobieskiSat


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
sitio

n

3
A

v

aila

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
olle

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
midit

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
al d

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
al d

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
t lo

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
eivin

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
ellin

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
cial m

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
elin

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
w, P

ola

n

d, 1

3.0

1.2

0

1

9

1

# 1. Changelog

- PDR
- Initially we planned to use an outside communication module with a chip supporting LoRa, but since it is already in CanSat kit provided to us, it was deemed unnecessary and we opted to came with some other ideas for the secondary mission.
- As of the PDR, our main goal in the secondary mission has changed. Now we are going to collect humidity and video data alongside PM density.
- In addition to the main goal of the secondary mission we also added plans to develop a descension assistance system (DAS).
- CDR
- We decided to leave out the camera because we could not find any suitable one for our needs and compatible to our board.
- We’ve updated our component list with final components we chose according to our financial capabilities and electrical requirements.
- Mission stages from PDR were modified due to software development.
- DAS (Descension Assistance System) was delayed due to prototyping restrictions and ultimately its goal was changed to predict the landing site using linear regression
- We found that LM35 thermometer was outputting unusable disturbed data while sending via radio. Because of that we use BMP280 as our main thermometer.
- We changed GPS module to Adafruit Ultimate GPS, it includes RTC module so one planned in PDR is not needed anymore.
- Particulate matter sensor was changed to SPS30

# 2. Introduction

## 2.1. Team composition

Our team consists of 5 students and our tutor, all of us are attending High School No. 2 named after King John III Sobieski in Kraków. Aleksandra Musiał - Our tutor, CS teacher and also an administrator at our school’s 3d printing laboratory.
- Jakub Czarny - Team leader & Electronic designer. His primary role is managing our progress and mission but he also specializes in electronic design and is responsible for choosing components according to our financial and electrical constraints. He is also our 3D designer.
Kraków, Poland, 13.01.2019 | 2

- Andrzej Szablewski - PR spokesperson, he takes care of all PR related missions like finding sponsors and managing and updating our site. He also works on 3D modelling and testing.
- Maciej Gamrot - High-Level Developer, he is responsible for main system development and communication with ground station. He also works on machine learning, look after our repository and develops our website.
- Damian Legutko - Embedded Developer, his job is to write code for managing data retrieved from sensors, designing backup procedures. On top, Damian designs graphical parts of our project when needed.
- Krzysztof Parocki - Hardware Engineer, he is responsible for electronic design, testing prototypes and overall design of the construction. Krzysztof makes photo-documentation of our progress, and makes a movie based on our creation process to promote our project in social media.


## 2.2. Available resources and time management

We’ve established cooperation with our school that provided us a classroom, where we hold our meetings and 3D printing lab that is under our tutor’s management. We have access to all the tools needed for the project in a public workshop - Hackerspace Kraków. Outside of the school we work on our own as well as in group through communication apps like Messenger and Discord. We meet once a week in our classroom to summarize the previous week and divide tasks for the next few days.

## 2.3. Mission overview

### 2.3.1. Primary mission

We’ve met almost all criteria for completing the primary mission. All we have left to is completing the parachute test it with our case design.
We completed tests of communication and were able to transfer all necessary data: pressure, temperature and elevation. At our range tests we we were able to transfer location at a range of 2.8km through obstacles (buildings and land elevation) and stopped not because of loss of signal but because of time restrictions. Our highest recorded RSSI was about -129 so we expect only better results in further tests.
We have completed our first design of the case and 3D printed it and following iterative design we will have more prototypes in the future to ensure our final case is up to our needs.
The electrical design is fully tested, functional and ready for secondary mission upgrades.

CanSat mission is divided into few stages. Because of the importance of primary mission, mission stages are dependent on the time from hardware oscillator clock and photoresistor, secondary mission readings are used only as reference.
- Initialization
During Initialization, software will diagnose every component and save received data in log files on SD card. Checking if everything is working properly would prevent from errors that might occur during the mission. In this stage Can should be standing still on a flat surface for about 3 seconds because few sensors inside would be calibrating.
- Await
The Can will wait for being placed inside the rocket. Probe will occasionally collect sensor data and photoresistor readings will indicate if is put in tray and trigger next stage.
- Launch
Except for light intensity, acceleration values from IMU module would be used as reference to mission stage. Sudden acceleration during lift might cause electrical components to behave in unexpected way, to avoid possible errors most of them will go into sleep mode. If Can could not receive any data after estimated time goes into next stage.
- Fall
As a main part of primary mission, in this stage probe will collect data from all sensors, save them to SD card and send via radio.

- Recovery
Probe goes into recovery stage after estimated time or when it detects landing via accelerometer or gyroscope. It waits to be found by searching team but still is collecting data used in secondary mission.

### 2.3.2. Secondary mission

Our main goal in the secondary mission is to gain first information about disasters and also volcanic activity. Our idea in case of volcanic activity is based on dropping the satellite inside the volcano, while it’s dormant.
Particulate matter density and humidity can be used for controlling and predicticting volcanic activity. Particulate matter is a very important factor in our secondary mission. Dust intensity determines chances for survival for both animal and human beings. High densities are very dangerous for life and are a direct information that the region needs evacuation. Other factors like temperature and humidity are also important as an information about life conditions. Our system can be used in fires as well as other natural disasters. The whole probe is supposed to output the collected data for the processing to happen on ground. This allows us to quickly adapt to whatever is needed and analyze the data thoroughly.
As for launching the probe in finals we expect to test all systems and check for errors as we don’t predict the army range will output dangerous data signalyzing any disasters. The whole point of the probe is life-sensitive data collection which can be interpreted in many ways.
In addition we will use landing site prediction software to help us understand where we are measuring and assist the primary mission recovery.

# 3. Probe description

## 3.1. Introduction

The whole probe will fit in a 3D printed case. Our list of electrical components is now final when it comes to primary mission components and matches our needs and requirements. Every planned sensor and its function is described below.

## 3.2. Components description

### 3.2.1. Microcontroller board

We managed to test the CanSat Kit microcontroller board and decided to use it inside the probe due to its big capabilities. It completely fulfills our needs and no board change is needed.

Current status: Tested and ready for final assembly

### 3.2.2. Batteries

We chose to go with 2600mAh modules (ICR18650-26FM) because we found a particular seller which would pre-weld them to a tin strip resulting in a 3P configuration of 7800mAh. This is still a massive battery pack that after a few hours of testing communication its voltage went down just 0.04V and will surely last long enough for the whole flight.

Current status: Tested and ready for final assembly

### 3.2.3. Atmospheric pressure sensor

This sensor fulfills all primary mission data gathering requirements, from received data we are able to calculate altitude of falling Can. The BMP280 provided with the CanSat Kit works just fine through the I

2C interface and we haven’t encountered any problems so far. It’s also working as our main thermometer, because it’s much more stable and calibrated than the LM35.

Current status: Tested and ready for final assembly

### 3.2.4. Particulate matter sensor

The particulate matter sensor is our main focus right now in the secondary mission. Basing on data collected from this sensor it is possible to examine life conditions. We opted for the SPS30 which provides us with not only higher accuracy compared to the PMS7003 chosen earlier but also a high sampling rate of 1Hz that erases the need for slower descension.

Current status: In shipment

### 3.2.5. Humidity sensor

Air humidity values would be used in secondary mission to predict possible fires. Very low humidity is often main cause of those disasters.
The DHT22 which we use to measure it has proven to be difficult to operate. It is causing board to behave in unstable way yet it update rate is very low. So far we could not find any better component to replace it.

Current status: Tested, possible upgrade planned

### 3.2.6. GPS module

We decided to buy the Adafruit Ultimate GPS module based on MTK3339 chip. It was more expensive than our initial choice but its capabilities and big community support made it a best option. It also provided us with a RTC powered by a backup battery.

Current status: Tested and ready for final assembly

### 3.2.7. IMU module

Accelerometer readings from this module could be used to predict earthquakes and avalanches.
Additionally IMU module will give us information about Can momentum additionally it is very useful during tests. We plan to use it when determining landing spot.
With use of special library we managed to get it working as intended. Kalman filters and Magdwick algorithm used in the library give us very accurate data but we need to convert it into a form that satisfies our needs.

Current status: Tested, needs software upgrade

### 3.2.8. Buzzer

Buzzer will help the search team in locating the Can on the ground after finishing the mission. Sounds made by it can exceed 85 dB, and definitely would be heard by search team.

Current status: Planned

### 3.2.9. Photoresistor

We can get information about CanSat mission stage in a very tricky way, thats by implementing photoresistor. When probe is outside the rocket it detects large amounts of light, if is inside a tray and is covered, no light shines onto photoresistor. So far we don’t need it and that is why we have not included it inside out prototypes.

Current status: Planned

## 3.3. Measurements

Table below presents data that will be gathered during the mission. Minimum and maximum columns represent predicted values to be received. Readings precision is presented in Significant figures column with format: [before ; after decimal point] in base 10.
Sensor | Reading variables | Minimum | Maximum | Significa nt figures | Samplin g time [ms]
BMP280 (I 2C) | Pressure | 600 hPa | 1100 hPa | 4 ; 1 | 40
| Temperature | -10°C | 30°C | 2 ; 1 | 40
Adafruit Ultimate GPS (UART) | Latitude | -24,09° | -14,07° | 2 ; 4 | 1000
| Longitude | 49,00° | 54,50° | 2 ; 4 | 1000
| Altitude | 0 m | 3000 m | 4 ; 1 | 1000
| Clock | mission start time | mission end time | - 1000
DHT22 (Digital communication) | Humidity | 0 % | 100 % | 2 ; 0 | 2100
| Temperature | -10°C | 30°C | 2 ; 1 | 2100
SPS30 (UART) | Mass concentration | 0.3 μg/m³ | 10 μg/m³ | 1 ; 1 | 1000
| Number Concentration | 0.3 1/cm³ | 10 1/cm³ | 1 ; 1 | 1000
2C) MPU 9250 (I | Tilt | 0° | 360° | 3 ; 2 | 10
| Acceleration | 0 g | 4 g | 1 ; 2 | 10
| Magnetic | 0° | 360° | 3 ; 0 | 30

## 3.4. Mechanical design


| orientation
Photoresistor (Analog) | Light intensity | 0 lux | 10 lux | 1 ; 2 | 10

### 3.4.1. Weight

We are almost sure that
the whole weight of the can and the parachute will be in a required range (300-350g). On this day our can weigh exactly 282g. We estimate use of about 0.62m² parachute material with an area density of 38g/m² — the parachute will weigh about 24g. Beside that we need few more components — about 30g.
Totally - 336g.

### 3.4.2. Case

We have decided to use ABS based filament called Z-UltraT for 3D printing the case, because it’s very strong and light. The parachute will be made from a professional grade material - Skytex 27 Classic. 3D design of the case is being done completely in Autodesk Fusion
360. Since PDR we went through 4 different design concepts of which 2 were 3D printed for development purposes and final concept testing. We plan to perform strength tests really soon and update the final design accordingly. Since our only available material is based on ABS it’s unlikely the case will fail.
The current status of our 3D designs can be found in attachments either in .f3d or .step files.
Because we are following the iterative design process these models are only concepts which were 3D printed for prototyping but will be improved with further testing and printing.

### 3.4.3. Parachute

We performed several tests of our first prototype parachute made from a precisely cut plastic foil at a diameter of 50cm, which resulted in maximum speed of 7.5 m/s after falling from 15m.


This was done after overestimating the necessary diameter of the parachute and allowed us to move on to the next version made from the material provided by one of our sponsors.


According to our calculations our parachute should be about 36 cm in diameter but after adjusting for the center hole version 2 of the parachute will be 40 cm. After tests of version 2 we will be able to adjust accordingly.

### 3.4.4. Transmitting antenna

For the transceiving antenna on the can we used a 17 cm long solid core wire soldered directly into the microcontroller board. So far it suited its purpose but in case of it being not enough we can replace it with a manufactured one.

## 3.5. Electrical design

### 3.5.1. Prototyping board design

Here is the schematic of a board we used for development:


And here is our final design that features only components we settled on:


### 3.5.2. Power consumption

Here is the theoretical maximum power consumption e.g. worst case scenario.
Component | Maximu m current draw [mA] | Voltage [V] | Efficiency 2 [%] | Effective power [mW]
Microcontroller | 20 1 | 3.3 | 50 | 132
SX1278 | 120 | 3.3 | 50 | 792
BMP280 | 1 | 3.3 | 80 | 7

SPS30 | 80 | 5 | 80 | 500
DHT22 | 1.5 | 5 | 80 | 9,4
Adafruit Ultimate GPS | 25 | 5 | 80 | 156,3
MPU9250 | 3.7 | 3.3 | 50 | 24,4
Total | 251,2 | - | - | 1621,1

Buzzer is only going to operate at the end of the mission.
Photoresistor is drawing an unnoticeable amount of current so we decided to skip them in the calculations

1 - Here we used the average values provided in the CanSat Kit documentation, because we think they are more suitable and we couldn't find the maximum power draw for the microcontroller.
2 - Efficiency is based on which power source is used by the component and it’s either 80%(Efficiency of the step-up converter) for +5V or ~50%(80%*66% -combined efficiency of the step-up converter and line regulator) for +3.3V

Battery capacity = 2600mAh*3*3,7V = 28860 mWh Total power consumption = 1621,1 mW Theoretical maximum operational time = ~17,8h

## 3.6. Software design

### 3.6.1. System structure


Main body of CanSat software is a Manager


object, it defines mission stage and distributes program time between all classes inside probe. It decides for example when to save sensors buffers to SD card or send them via radio. While developing software we found out that board crashes if some of instructions are send one after another, Manager cares to not invoke such incidents by leaving proper time intervals between those instructions and is responsible for error handling if they occur.
For every sensor inside probe, there is a class with defined data reading methods that inherits from abstract Sensor class.
Sensor class consists of initialization and update methods, radio and SD buffers, diagnosis variables and update time. Software structure like this allows to use every sensor in unified way without worrying about it's other methods required for proper working.

### 3.6.2. Data gathering

Every sensor has different specifications and by that every has its own update time, to not lose data while waiting for those with low sampling rate, sensors are invoked dynamically by Manager when their update time expires. With every measurement sensors input new reading into their SD buffer and every reading is marked with hardware clock time. For example BMP280 saves pressure and temperature
floats and GPS saves last received NMEA sentence.
Methods responsible for data gathering are
different for every one of them but their outputs are later unified to fit Sensor base.
SD card contains separate .txt files for each sensor. Every measurement occupies a single line with a time marker at its end. Example file is presented on image on the left.

### 3.6.3. Event logging and timers


Our CanSat software implements functions responsible for logging too. Every important action inside probe will be saved with time marker on .txt log file.
By time marker in CanSat we understand millis() function that returns amount of milliseconds elapsed since board start returned by hardware clock. Additionally software gets current time from RTC module inside GPS board, at the beginning of log file there is an information about real time and time marker.
Example heading of a log file: #110119161503412@1302
This string lets us know exact day, month, etc.. and time marker during this moment (number after @ char). Every action after this line will be marked only with time marker because we can simply add difference of elapsed milliseconds to get event time.

### 3.6.4. Radio transmitting

So far during our tests we have transmitted data in the standard way, that is by sending values in decimal form in strings.

During tests we found packet of length 47 bits as most optimal transmission configuration. It gives us about 2 transmissions per second with 97B/s speed.
In the final version we plan to send compressed values based on measurement estimated value range and its binary representation. Data values collected from sensors would be mapped to some binary number with length specified by reading precision. For example knowing that temperature is in range of -10 to 30°C and reading precision is: two digits before and one after decimal point, we can map value from 0 as -10.0°C up to 400 as 30.0°C. Numbers in that range can be represented as binary number with length of 9 bits. While sending string like: ‘14.2’, 4 chars are send and that is equal to 32 bits. In this case we have compressed our data by factor of about 3.5!

# 4. Ground station

## 4.1. Radio receiving

Antenna:
Our base station antenna (LPRS | YAGI-434A) | was ordered from UK and
works without any problems. We had to design a handle and print it on a 3D printer. After installation it performs exactly as intended. It already was equipped with an SMA connector so no modifications were necessary. Its aluminium construction makes it very light and easy to handle which helps make it handheld.

Data received by the receiver will be outputted to a serial port in raw form. Software ran on the computer connected to the receiver via USB will listen for input. Read data will by parsed, displayed and subjected to further analysis. Each input will be also saved by EventManager both in parsed and raw form. Example file by EventManager:


## 4.2. Ground Station Interface

We divided main window of ground station graphical interface into a few groups:
- Information Board display live information from satellite (temperature, humidity, etc)
- Interactive Gyroscope Widget informs about the inclination of satellite relative to the ground by processing data from GPS
- Interactive Map Widget plots current and past location of satellite creating the flight path of our satellite. Each point is colored depending on RSSI and can be clicked to display further information about satellite at that moment. We also plan to add landing zone prediction feature using machine learning based on location, speed, acceleration and wind strength.
- Group of buttons used to control the software (work in progress)
- Interactive graph plotting live data from satellite (work in progress)


### 4.3. Landing prediction feature

We plan to implement landing prediction feature into our ground station software. So far we found linear regression methods as the best candidate. From received GPS data we are able to represent the Can’s route as a line in three dimensional space. Having known ground altitude we can solve the linear equation and get the predicted landing position. The results definitely would not be very accurate, in the future we plan to also use IMU data providing we find proper methods to use them.

### 4.4. Noise Cancelling

During tests, we discovered that some data packets were corrupted during long-distance data transmission, so we decided to develop specialized software that could recognize these corrupted packets based on previous one. We also consider using machine learning for this since we have access to a large amount of data.

### 4.5. Data Analyzing Software

After flight probe can be plugged to the computer for analyzing information saved on SD Card. Software will recognize connection and enter Debug Mode in which every measurement will be plotted in a window similar to the one with live data, but with feature to reenact flight history in a real time and readout by readout. All information will also be compared and analyzed with regard to irregularities and interferences.

# 5. Project summary

## 5.1. Resource management

### 5.1.1. Budget and costs

Note: All prices in this section are converted from PLN to EUR with exchange rate 1 PLN = 0.232996887 EUR (05.01.2018 - Google)

We have started with 267,95 EUR. We hope we will get more money and partners. Now we are on a good way to get a sponsorship from Kraków Airport. On this day (05.01.2019) our spending is presented in the table below.

No. | Thing we have bought | Price (EUR) | Category
1. | website hosting | 4,66 | Promotion
2. | Facebook advertisement | 5,82 | Promotion
3. 2x Charger TP5056, 2x Buzzer, 1x DHT22 and | shipment | 7,47 | Modules
4. 1x MPU9250 sensor, 3x batteries, welding service | and shipment | 21,64 | Modules
5. | 1x Adafruit Ultimate GPS and shipment | 38,09 | Modules

6. | Antenna and shipment | 53,42 | Modules
7. | Electrical tape, sandpaper | 1,05 | Modules
8. | Food, snacks, drinks for meetings | 31,43 | Meetings
| SUM | 163,58

Now we have 267,95 - 163,58 = 104,37 EUR. We have already bought everything we need except few parts. Our estimated expenses are: few more modules and eventually cost of the participation in the final for the fifth member of a team.

### 5.1.2. CanSat Value

Note: All prices in this section are converted from PLN to EUR with exchange rate 1 PLN = 0.232996887 EUR (05.01.2018 - Google)

The whole value of our CanSat is presented in the table below.

No. | CanSat part | Value (EUR)
1. | Adafruit Ultimate GPS | 34,92
2. | Batteries and welding service | 11,87
3. | MPU9250 | 7,69
4. | DHT22 | 3,69
5. | Buzzer | 0,47
6. | Li-Ion Charger | 1,21
7. | SPS30 | 40,93
8. | Case - 80g Z-ULTRAT material | 4,66
9. | Parachute and cords | 5,00
| SUM | 110,44

### 5.1.3. Sponsors

Note: All prices in this section are converted from PLN to EUR with exchange rate 1 PLN = 0.232996887 EUR (05.01.2018 - Google)

We wanted to amp up our chances for getting a sponsor so we have written to the following companies:
Comarch, Asseco, Cd projekt, Orange, Play, Coca cola, Pepsi, Rmf fm, Ailleron, Shell, Orlen, Lotos, Arge, Tvn, Radio zet, Tok fm, Kraków Airport, Codewise, Flytech UAV, Kraksky, botland.pl, School parental council, Company which want to be anonymous.

We have several sources of money as well as partnerships. They are presented in the tables below.

No. | Source of money | Amount (EUR)
1. | School parental council | 186,40
2. | Team contribution | 58,25
3. | Team advisor contribution | 23,30
| SUM | 267,95
No. | Partnership | Our benefits
1. | Our school | We have unlimited access to our school’s 3D printing lab
2. | Botland.pl | We got a 7% discount on all their items
3. Company | which wants to be anonymous | We got parachute material and parachute cords -The material is called DOKDO-N20DMF-WR-HD38
4. Kraków | Airport | We are on a good way to get a sponsorship from Kraków Airport. All we need now is an official confirmation from CanSat organizers about safety and other regulations of the satellite launch.

## 5.2. Schedule

No. | Date | Planned action
1. | 17.01 | Finishing Parachute
2. | 19-20.01 | Testing Particulate Matter Sensor
3. | 25.01-5.02 | Final development and designing final case
4. | 10.02 | Printing final version of the case
5. | 10.02-20.02 | Adjusting all components and writing final code
6. | 20.02 | Fitting all components in the can, building it ultimately and checking weight
7. | 25-28.02 | Ultimate tests of communication, transmitting data, parachute and checking if all components work together without any problems
8. | 02.03-9.03 | Ultimate trials of everything and writing FDR
9. | 10.03 | FDR

## 5.3. Documentation

### 5.3.1. Social media & promotion

We have over 300 likes on our Facebook account (linked below). Posting regularly 20 posts, we have on average 400 views under every single one. We have also several posts with about 1000 views, and also one, promoted, with nearly 8000. This post is a movie-type which is a vlog from our first radio transmission tests. By doing this, we wanted to promote our project as well as the whole competition among the local and school community. Due to the project promotion we hope we will get more partners. Beside that we promoted ourselves on our schools facebook group which has over 3000 members.

Facebook site: https://www.facebook.com/SobieskiSat/

### 5.3.2. GitHub Repository

We decided to create a public organization in github, so that everyone interested in our project could follow our progress. You can find there the entire code of the satellite and ground station. We also include all 3D models, diagrams and documents of our project. This helps to organize and archive all of our work, enabling easy tracking.

Our GitHub: https://github.com/SobieskiSat

### 5.3.3. Timeline

### 26 September – The date of one of our first actions taken to

develop our micro-satellite. This day we finally got access to the school 3D lab, where we printed the first case to see exactly how much space we do have to fit in all components. We have also mentioned this action in PDR, as one of the Project Summary.


### 30 September – that day we met with the airplane pilot, who

helped us to design and plan a lot of thangs attached to aerodynamics and electronic circuits. We elaborated a project of components composition inside the case, spoke a lot about secondary mission idea and chose the way which our marketing and advertising actions will follow in the future.


### 20 November – our first meeting

during which we were testing modules we had received a couple days before. We have tested
components | such | as
accelerometer, | gyroscope | and
magnetometer, | simultaneously
with | other | essential modules
needed to complete the primary
mission. All gages of these we


have done on a breadboard, but after that we still needed to wait for missing parts.

### 27 November – that was our second meeting during which we

worked with modules, provided to us a few days after the first meeting. We finished the attunement of the GPS module, and we plugged in the same time every other module to see if it will work correctly – the only one missing was particulate matter module, which we planned to add and trial at one of our future meetings.



### 11 December – Our measures to

design a first prototype were over. We printed a new case for our modules, this time it was more durable and contained a top, so that we could close components up inside. We fitted in all modules needed to complete primary mission and some from secondary and wrote a code to be able to send data from the can and receive it in our ground station, so the first prototype was finally ready to try.

### 13 December – we got an high-range aerial ordered a week

before, that we needed to receive data from our can and relay it further to the ground station. We did a few adjustments in our code to meet the aerial requirements and make everything work correctly, and decided that we need to probe the real aerial range to check if the signal will work during the final competition.


### 18 December – The day of trials. We were testing our aerial range

for about 4 hours, by leaving the ground station in the northernmost part of Błonia, and walking away as far as we could with our sender.

We have reached 2,8 km distance, without a big loss of signal, hence we were certain that out satellite will be transmitting data all the time during the plummeting at the finals. That day we have also completed our stab at cansat falling with parachute. Full report of our efforts was posted on our facebook page as a vlog and animation of our repositioning


### 23 December – The first usable prototype of the parachute was

done. All measurements and calculations had been completed, and afterwards the plastic foil was cut and formed.
Work on the code was also going forward that day


### 8 January – We have 3D printed a new version of the case with

some improvements, for example holes to provide better air-circulation and new latch system to test new ways of joining the two halves. We have also thrown it with a parachute out of a balcony to check if it will fall properly without destroying itself.


### 11 January – Parachute material was finally with us, provided by

the company which wants to stay anonymous – we got over six times more material than we wanted, which enabled us to make multiple versions and test each one separately. We’ve also set up our Github page


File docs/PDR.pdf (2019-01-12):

# Preliminary Design Review

for CanSat competition

Team

## SobieskiSat


04.11.2018 Kraków, Poland

## Table of Contents

Changelog | 3
Introduction | 3
Team overview | 3
Team composition | 3
Resources and time management | 4
Team promotion | 4
Secondary mission overview | 5
Probe description | 5
Introduction | 5
Mechanical design | 5
Electrical design | 6
Software design | 7
Project summary | 10
Current project phase | 10
Printing CanSat case: | 10
Successful primary mission tests: | 10
First positive sponsor response: | 10
Resource management | 10
Challenges and problems | 11
Schedule | 11
Kraków, Poland, 04.11.2018 | 2

## 1. Changelog

- Initially we planned to use an outside communication module with a chip supporting LoRa, but since it is already in CanSat kit provided to us, it was deemed unnecessary and we opted to came with some other ideas for the secondary mission.
- As of the PDR, our main goal in the secondary mission has changed. Now we are going to collect humidity and video data alongside PM density.
- In addition to the main goal of the secondary mission we also added plans to develop a descension assistance system.

## 2. Introduction

## 2.1. Team overview

- Team composition
Our team consists of 5 students and our tutor, all of us are attending High School No. 2 named after King John III Sobieski in Kraków. Aleksandra Musiał - Our tutor, CS teacher and also an administrator at our school’s 3d printing laboratory.
Jakub Czarny - Team leader & Electronic designer. His primary role is managing our progress and mission but he also specializes in electronic design and is responsible for choosing components according to our financial and electrical constraints.
Andrzej Szablewski - PR spokesperson, he takes care of all PR related missions like finding sponsors and managing and updating our site. He also works on 3D modelling.
Maciej Gamrot - High-Level Developer, he is responsible for main system development and communication with ground station. He also develops our website.
Damian Legutko - Embedded Developer, his job is to write code for managing data retrieved from sensors, designing backup procedures. On top, Damian designs graphical parts of our project when needed. Krzysztof Parocki - Hardware Engineer, he is responsible for electronic design, testing prototypes and overall design of the construction. Krzysztof makes photo-documentation of our progress, and makes a movie based on our creation process to promote our project in social media.


- Resources and time management
We’ve established cooperation with our school that provided us a classroom, where we hold our meetings and 3D printing lab that is under our tutor’s management. We have access to all the tools needed for the project in a public workshop - Hackerspace Kraków.
Outside of the school we work on our own as well as in group through communication apps like Messenger and Discord. We meet once a week in our classroom to summarize the previous week and divide tasks for the next few days.
- Team promotion
We are looking for a sponsor - we wrote emails to a variety of companies including local industries and big foreign concerns. We are also going to put an announcement on our facebook profile that we are looking for a supporter. We have our own website written in both polish and english. Also we launched the facebook site where we have now almost 200 likes. We will use our media for sharing the progress of building the satellite as well as presenting some interesting facts or showing photos and short movies. There you can follow us and our actions:
- Facebook: https://www.facebook.com/SobieskiSat/
- Website: https://www.sobieskisat.pl/

## 2.2. Secondary mission overview

Our main goal in secondary mission is to collect humidity and particulate matter density data alongside a video feed and positioning to complete a thorough analysis of its surroundings. Gained information would be later analyzed for life sustainability.
Descension Assistance System (DAS)
Our second goal is to develop a | neural network | for controlling descension,
ultimately leading to landing in a pre-specified area. Servos inside the Can will pull the strings attached to a parachute causing a shift of the centre of mass, that should change body momentum. If control over the probe fails we hope to at least receive predictions as to where it’s going to land.
Both sensor readings and DAS together might be used in autonomous missions to other planets in search of an extraterrestrial life.

## 3. Probe description

## 3.1. Introduction

We managed to test the CanSat Kit microcontroller board and decided to use it inside the probe due to its big capabilities. The whole probe will fit in a 3D printed case.
Components chosen for collecting data are:
- Temperature sensor - LM35
- Pressure sensor - BMP280
- Gyro, magnetometer and accelerometer - MPU9250
- Camera - OV7670 (subject to change)
- RTC module - DS1307
- PM sensor - PMS7003
- Humidity sensor - DHT22
- GPS module - NEO_6EM

## 3.2. Mechanical design

We have decided to use ABS based filament called Z-UltraT for 3D printing the case, because it’s very strong and light. The parachute will be made from a professional grade material - Skytex 27 Classic. Paratuche strings will be tied to gears inside the DAS but due to a risk of breaking, emergency strings will be attached alongside the main ones. We will have access to the internals through an opening made by dividing the whole case in half vertically. The two halves will be connected by screws or latches. In emergencies it will also be possible to use tape to temporarily close the case. We will try to minimize the use of steel screws in favor of lighter methods of connection.
Initial component placement is presented on image below.


## 3.3. Electrical design

The probe will be powered by 3 Li-ion cells, with 3000mAh capacity each, connected in parallel. By our calculations current draw for the whole can shouldn’t exceed 500mA at maximum load, so it should be able to run for about 15 hours.
We are working on a PCB for all of the loose modules and the first iteration is shown below. We are expecting to buy all components soon so we can test them out and resolve initial problems that may occur.


## 3.4. Software design

- Primary mission:
When turned on, probe will be waiting for USB Serial messages for debug & calibration. If no data is received probe will initialize awaiting mode. In this state CanSat waits for an interrupt signal from the launch switch and occasionally collects sensor values in order to save battery energy.
When launch switch gets pressed the mission mode is initiated, probe collects temperature and pressure data with sampling rate of at least 2Hz. Gained information is sent to ground station in packets marked by time from RTC module. All events and data will be stored in logs on an SD card.
After an estimated falling time probe goes into retrieving mode. Sound and radio signals are sent in order to help the search team with finding it. When launch switch is pressed again the probe turns itself off. Primary mission would be independent from the secondary mission except for accelerometer and GPS readings used as additional information about the mission phase.
- Secondary mission:
The probe in mission mode will collect sensor and positioning data. Neural network model used in DAS will be trained in a simulation in Unity3D. Model will require position, acceleration and tilt in three axes as an input, giving two values used for controlling servos changing direction of the probe.

Initial block diagram of primary mission is presented below.


## 4. Project summary

## 4.1. Current project phase

- Printing CanSat case:
First thing we did after
getting permission to use
our school’s 3D printers is printing a cylinder the size of a typical CanSat to help us better visualize the
placement of our planned
internal components.


- Successful primary mission tests:
One board sends pressure and temperature data to another, which then displays the received data on a computer screen.


- First positive sponsor response:
We managed to get in contact with the CEO of Allincard about sponsoring our project and after initial conversation we received a green light and are awaiting the final decision from the foundation's council. We expect to receive around 200 PLN (~46 EUR), which should cover our initial expenses.

## 4.2. Resource management

We have created spreadsheet with all components and their properties presented below.


By our calculations current CanSat price is around 130 EUR (73 EUR for primary mission and 57 EUR for secondary)

## 4.3. Challenges and problems

- Gaining money from sponsors
- Without further tests we are not able to tell if DES would work as we expect
- Long distance radio communication
- Metal PM sensor case may interfere with GPS and LoRa signals, if so 3D printed case would be needed
- Some of our components using the SPI and I2C interfaces require pull-up resistors to the 5V line, but the board already has them, but to the 3.3V line. This may force us to unsolder the resistors on the CanSat kit board.

## 4.4. Schedule

We have created a Trello timetable, here are few important dates from it:
- Buying all necessary components - 18.11
- CanSat on breadboard - 20.11
- Finishing parachute design - 20.11
- Successful primary mission test - 25.11
- Testing long distance radio communication - 01.12
- Testing DES system - 04.12
- First working prototype - 11.12
- Christmas break; time for testing can and writing CDR - 21.12 to 02.01
- CDR - 13.01

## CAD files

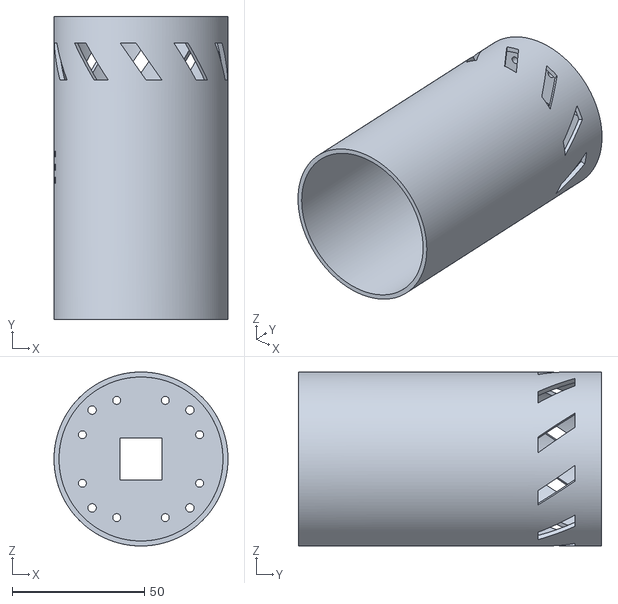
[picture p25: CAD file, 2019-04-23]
models/ZNICZ1_Cover.stl
65.8 x 114.6 x 65.8

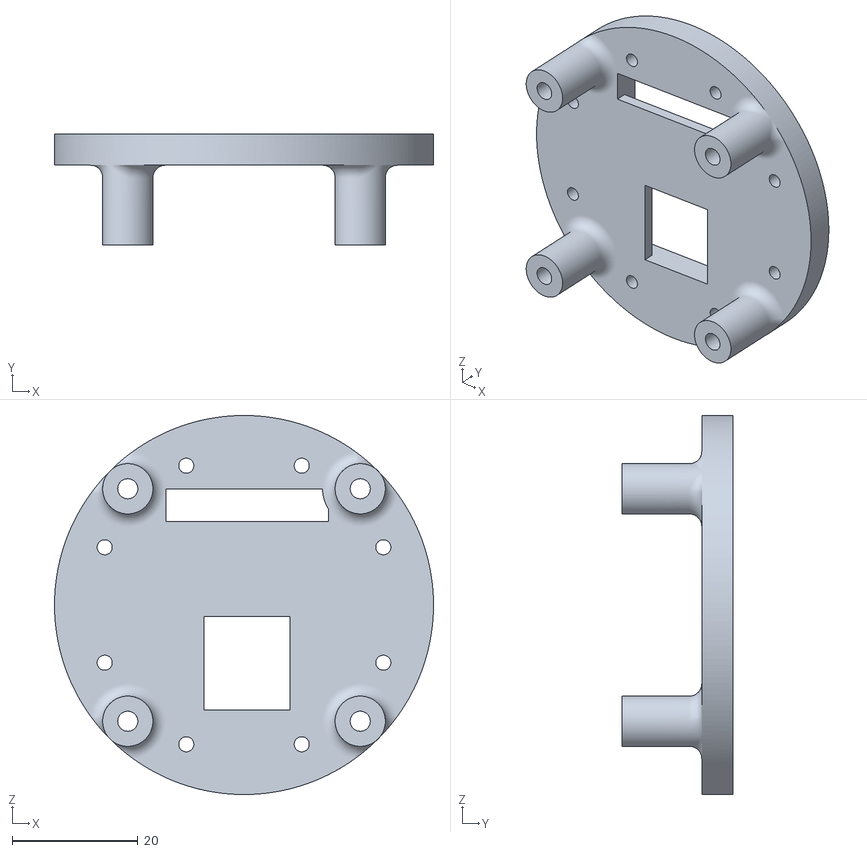
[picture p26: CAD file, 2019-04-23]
models/ZNICZ1_CoreGPS.stl
60.3 x 17.7 x 60.3

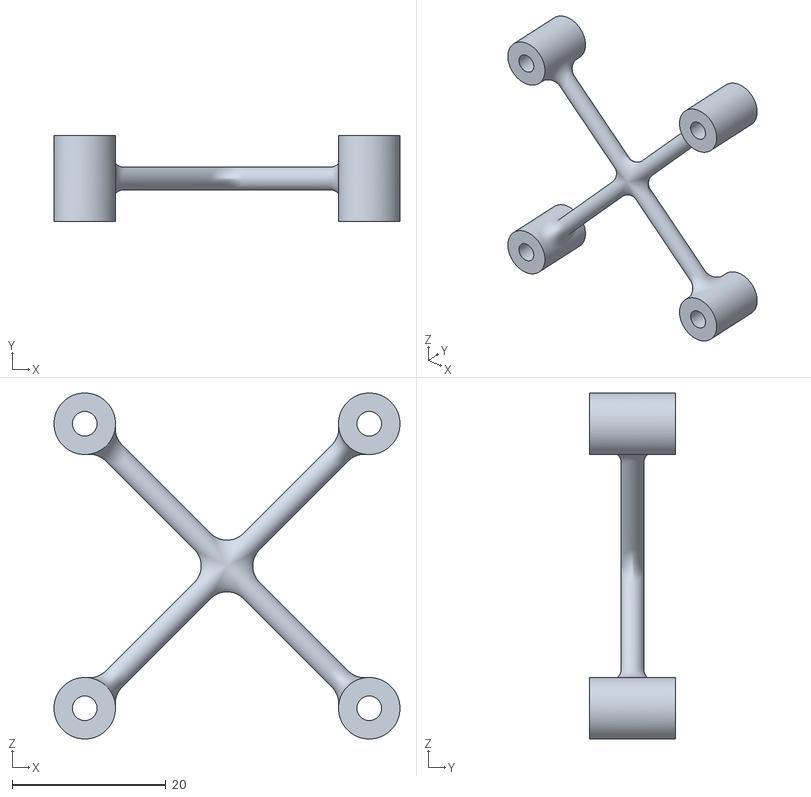
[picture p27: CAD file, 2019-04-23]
models/ZNICZ1_CoreStruct.stl
45.0 x 11.2 x 45.0

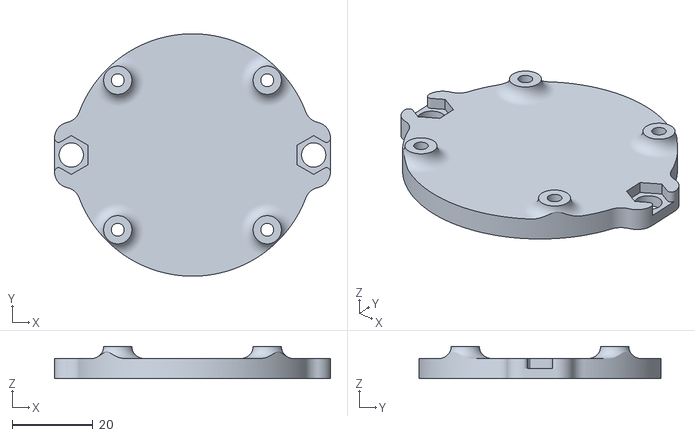
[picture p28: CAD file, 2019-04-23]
models/AH2_Holder1.stl
68.3 x 60.0 x 8.00

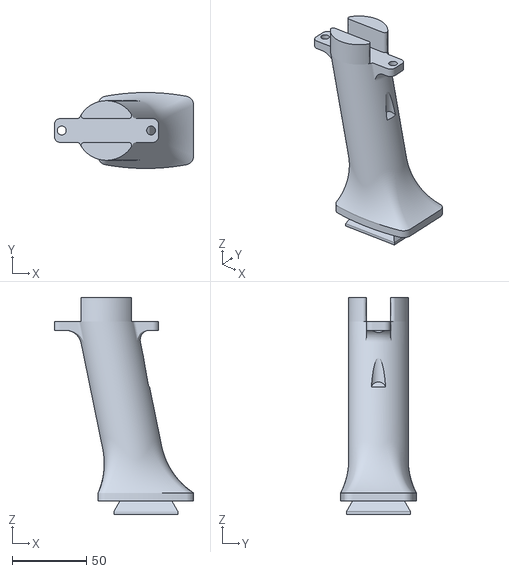
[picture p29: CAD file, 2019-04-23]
models/AH2_Handle2.stl
93.6 x 51.0 x 145.7

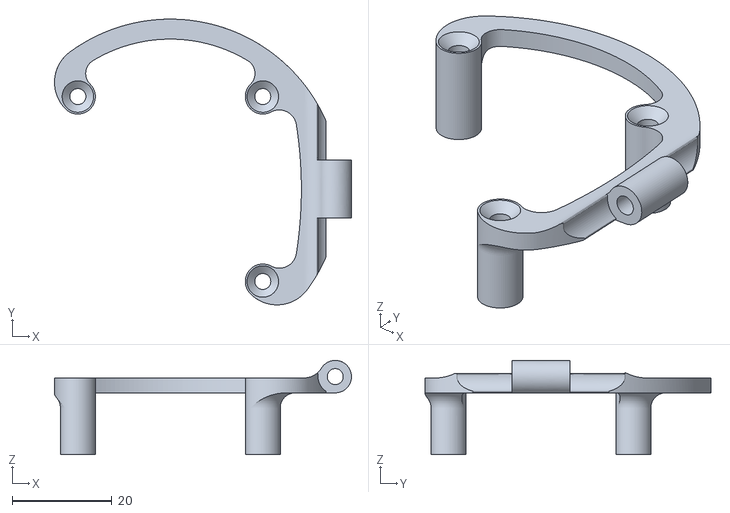
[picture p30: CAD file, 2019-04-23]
models/AH2_Holder2.stl
59.4 x 57.2 x 18.9

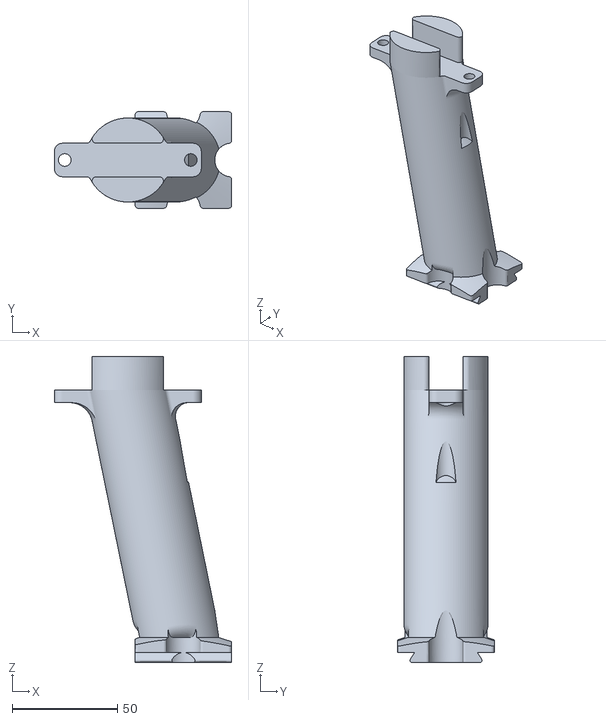
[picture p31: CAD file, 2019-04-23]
models/AH2_Handle.stl
84.5 x 46.0 x 145.7

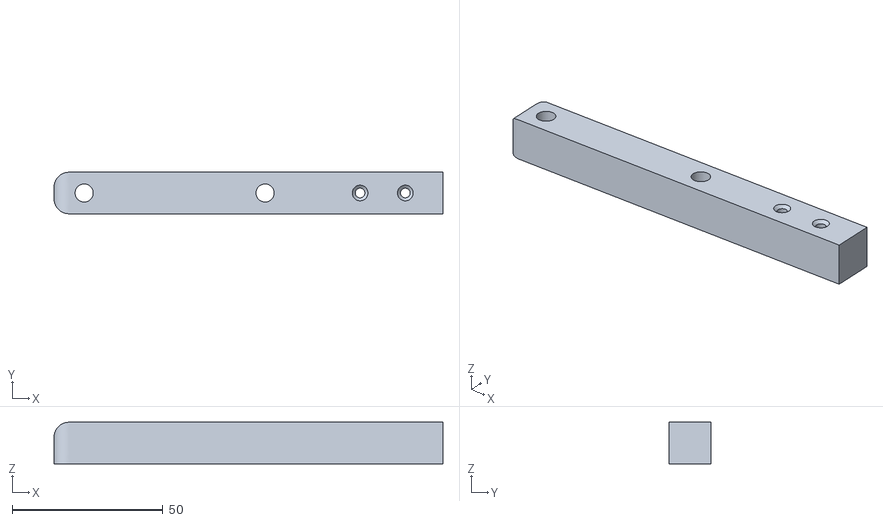
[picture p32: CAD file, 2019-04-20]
models/AH2_Counterweight2.stl
129.0 x 13.8 x 13.8

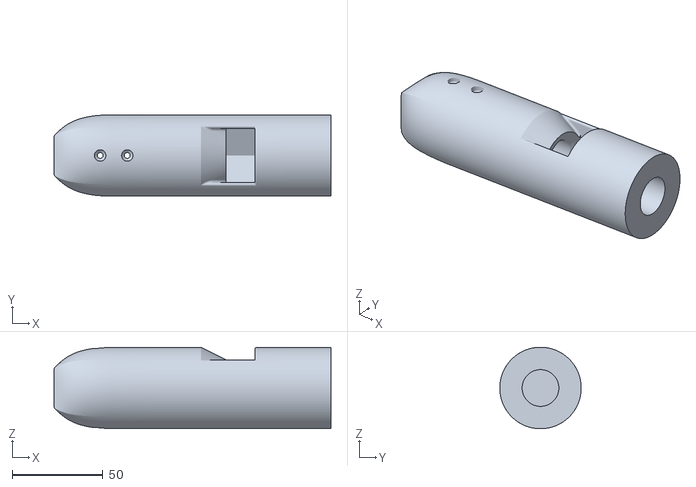
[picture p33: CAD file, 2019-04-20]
models/AH2_Counterweight.stl
153.0 x 45.0 x 45.0

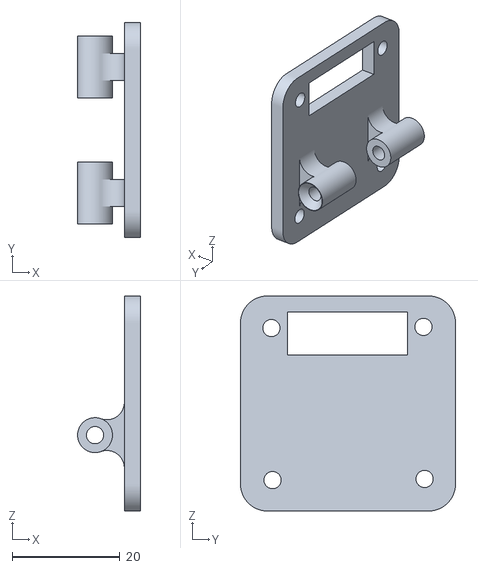
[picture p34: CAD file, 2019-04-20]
models/AH2_Holder3.stl
11.7 x 40.0 x 40.0

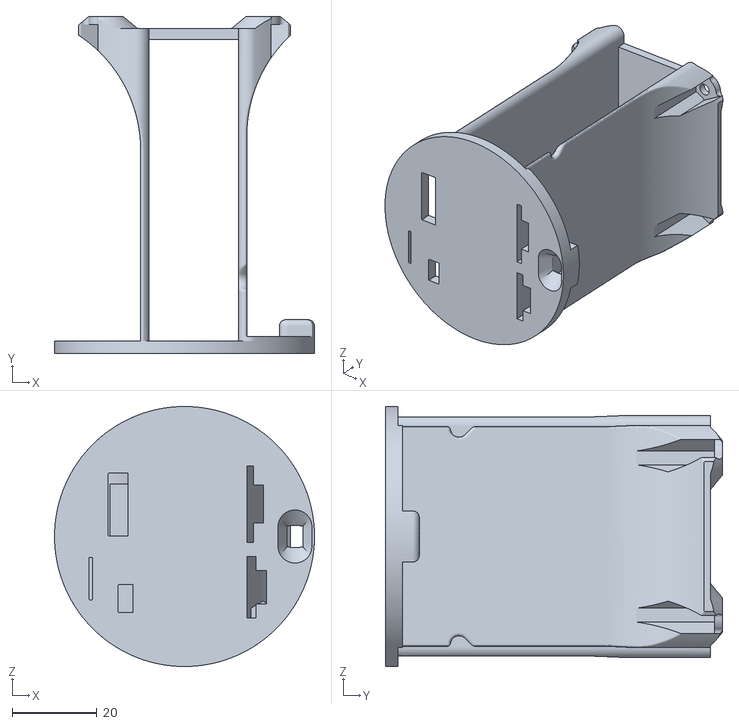
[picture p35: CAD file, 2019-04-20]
models/ZNICZ1_Core.stl
61.2 x 79.4 x 61.2

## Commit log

2019-01-12 Add Data
    [Antenna_handle-v8.f3d, Znicz1-v4.f3d, Znicz2-v4.f3d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]
2019-02-19 Added new design, ready for 40mm screws
2019-02-26 Added gerber files
    Gerber files of our pcb
    [Gerber_BoardOutline.GKO, Gerber_BottomLayer.GBL, Gerber_BottomSilkLayer.GBO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]
2019-04-20 Final release
    Fuck everything else, I won't change a thing in these now. Fuck your previous models and history, those are all we need
    [AH2_Counterweight.stl, AH2_Counterweight2.stl, AH2_Handle.stl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]
2019-04-20 Final Release
    [Gerber_BoardOutline.GKO, Gerber_BottomLayer.GBL, Gerber_BottomSilkLayer.GBO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]
2019-04-23 Minor changes
    new handle, slight adjustments
    [AH2_Handle.stl, AH2_Handle2.stl, AH2_Holder1.stl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]
2019-04-23 Compressed prints
